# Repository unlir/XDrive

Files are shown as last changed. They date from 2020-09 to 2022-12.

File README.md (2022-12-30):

# XDrive 
Stepper motor with multi-function interface and closed loop function.  
具有多功能接口和闭环功能的步进电机。
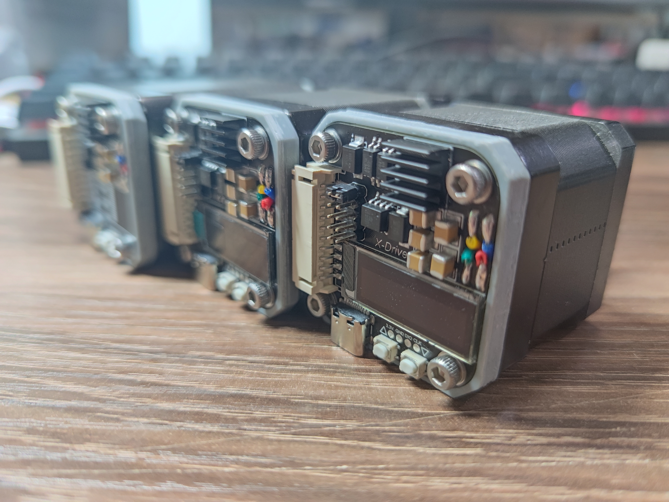
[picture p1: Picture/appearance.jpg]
appearance icon


## 版本更新日志
### 2021/01/03
1.避开了上电后第一次读取编码器错误数据造成的启动抖动（本质问题未解决）  
2.修正了控制器初始化错误造成的启动抖动（本质还是因为第一条的原因）  
3.XDrive_BL升级到F1.2版本，仅使用UP按键作为升级按键  
4.修正了一些讲不清道不明的BUG  
5.XDrive项目讨论可加群（3群：1105302151）（2群：1105489563）（1群：557214000）

## 目录简介
Firmware_APP：主要的控制固件（XDrive_APP.uvprojx 为主应用工程） 
Firmware_BL：引导固件（用于引导USB更新）  
Hardware：电路图纸  
Machinery：外壳图纸  
Picture：XDrive照片  
Specification：使用及入门介绍

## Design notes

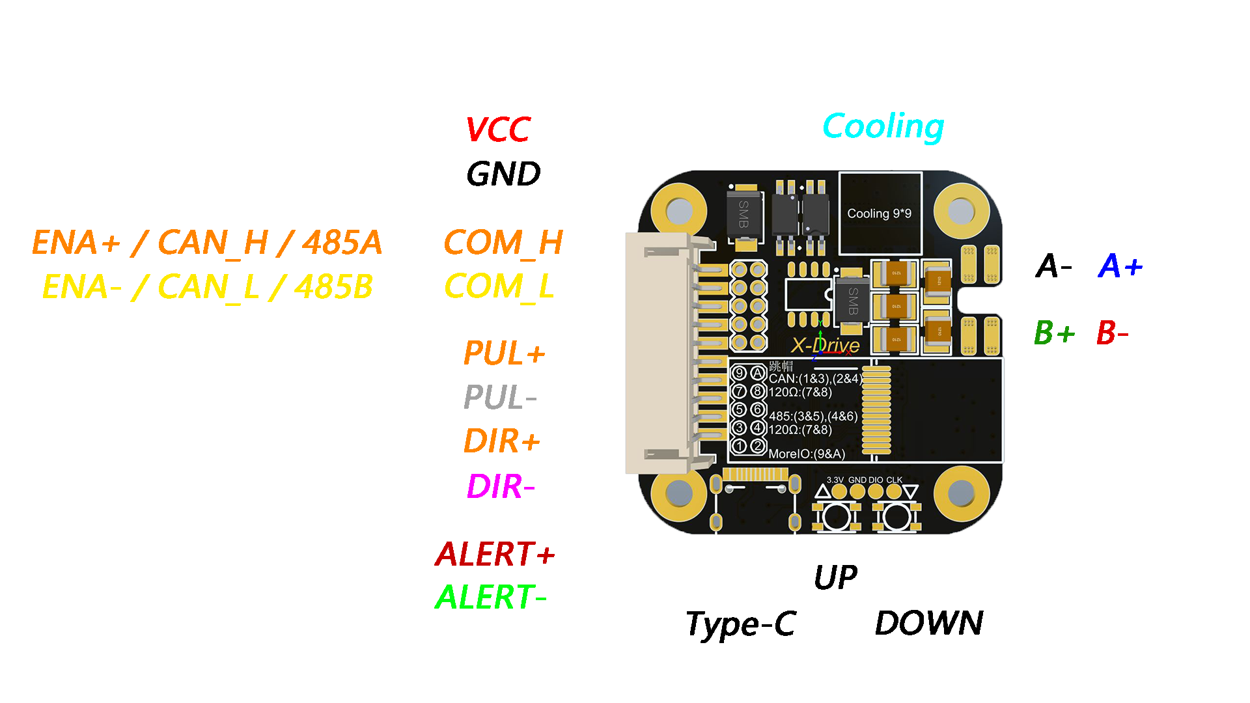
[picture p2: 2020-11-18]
Specification/输入输出标注.png

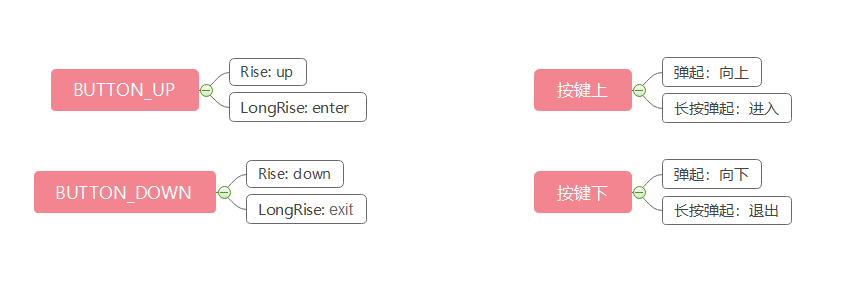
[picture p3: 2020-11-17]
Specification/Button.png

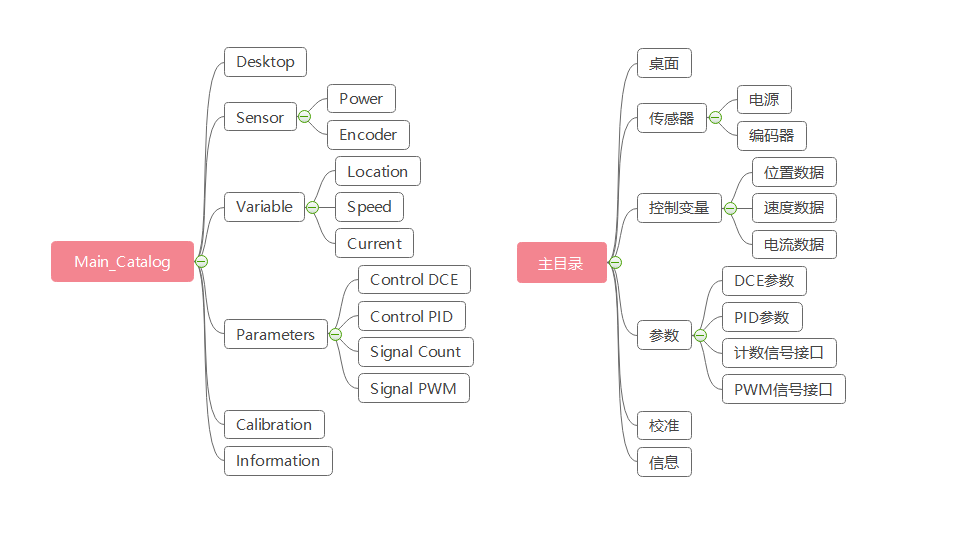
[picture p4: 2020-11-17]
Specification/UI Logic.png

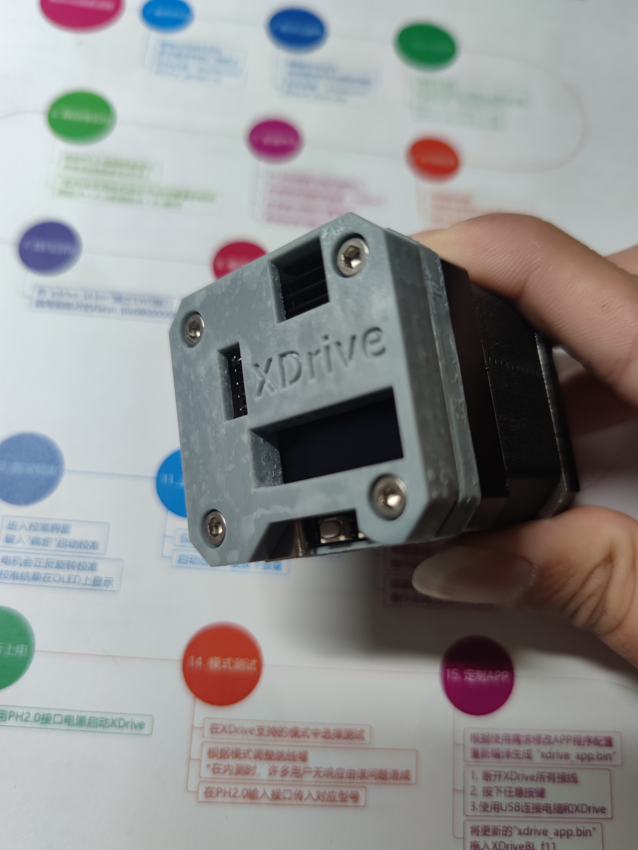
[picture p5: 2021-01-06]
Picture/shell.jpg

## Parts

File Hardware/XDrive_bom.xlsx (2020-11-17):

Comment | Description | Designator | Footprint | LibRef | Quantity | Pins
20pF (200) 5% 50V | 贴片电容 | C1, C2 | 0603_C | 0603 20pF (200) 5% 50V | 2 | 2
100nF (104) 10% 50V | 贴片电容 | C3, C4, C5, C6, C7, C8, C9, C10, C11, C12, C13, C14, C16, C17, C18, C19, C21, C22, C27, C29 | 0603_C | 0603 100nF (104) 10% 50V | 20 | 2
10uF (106) 10% 10V | 贴片电容 | C15, C23, C28, C30, C35, C36, C37, C38 | 0603_C | 0603 10uF (106) 10% 10V | 8 | 2
100pF (101) 5% 50V | 贴片电容 | C20 | 0603_C | 0603 100pF (101) 5% 50V | 1 | 2
47uF (106) 20% 10V | 贴片电容 | C24 | 1206_C | 1206 10uF (106) 10% 50V | 1 | 2
4.7uF (475) 10% 50V | 贴片电容 | C25 | 1206_C | 1206 4.7uF (475) 10% 50V | 1 | 2
1uF (105) 10% 16V | 贴片电容 | C31, C32, C33, C34 | 0603_C | 0603 1uF (105) 10% 50V | 4 | 2
100uF (107) 20% 50V | 贴片电容 | C41, C42, C43, C44, C45 | C 1210_L | Cap | 5 | 2
NC | 贴片电容 | C46, C47, C48 | C 1210_L | Cap | 3 | 2
双排插针-2X5P | 双排插针-2.0mm | CN1 | A2005WV-2X5P | A2005WV-2X5P | 1 | 10
SESD3Z12C | 双向ESD | D1, D2 | SOD-323 | SESD3Z12C | 2 | 2
SS54 | 二极管 | D3 | SMB | SMA(DO-214AC) SS54 | 1 | 2
B5819WS | 二极管 | D4, D6 | SOD-323 | SOD-323 1N4148WS T4 | 2 | 2
SMBJ28CA | TVS | D5 | SMB | SMB/DO-214AA P6SMB6.8CA | 1 | 2
SMD0805-020 | 自恢复保险丝 200mA | F1, F2 | FU 0805 | Fuse 2 | 2 | 2
SMD0805-050 | 自恢复保险丝 500mA | F3 | FU 0805 | Fuse 2 | 1 | 2
6.8UH 6R6 | 贴片电感 | L1 | L 1206 | IND | 1 | 2
OLED12832 | OLED焊接座 | L2 | PCBComponent_1 - duplicate | OLED12832 | 1 | 15
10KΩ (1002) ±1% | 贴片电阻 | R1, R2, R9, R24 | 0603_R | 0603 10KΩ (1002) 1% | 4 | 2
1KΩ (1001) ±1% | 贴片电阻 | R3, R4, R6, R7, R10, R14, R15, R17 | 0603_R | 0603 1KΩ (1001) 1% | 8 | 2
0.1Ω (R100) ±1% | 贴片电阻 | R5, R8 | 1206_R | 1206 0.1Ω (R100) 1% | 2 | 2
200Ω (2000) ±1% | 贴片电阻 | R11, R13, R16, R18 | 0603_R | 0603 200Ω (2000) 1% | 4 | 2
120Ω (1200) ±1% | 贴片电阻 | R12 | 0805_R | 0805 120Ω (1200) 1% | 1 | 2
22Ω (22R0) ±1% | 贴片电阻 | R19, R20 | 0603_R | 0603 22Ω (22R0) 1% | 2 | 2
1.5KΩ (1501) ±1% | 贴片电阻 | R21 | 0603_R | 0603 1.5KΩ (1501) 1% | 1 | 2
12KΩ (1202) ±1% | 贴片电阻 | R22, R23 | 0603_R | 0603 12KΩ (1202) 1% | 2 | 2
1.91KΩ (1901) ±1% | 贴片电阻 | R25 | 0603_R | 0603 1KΩ (1001) 1% | 1 | 2
1MΩ (1004) ±1% | 贴片电阻 | R26, R27 | 0603_R | 0603 1MΩ (1004) 1%, 0603 2MΩ (2004) 1% | 2 | 2
SKRPABE010 | 4脚贴片按键 | SW1, SW2 | KEY-SMD-4P_L4.20-W3.20 | SKRPABE010 | 2 | 4
STM32F103CBT6 | STM32 ARM-based 32-bit MCU Performance Line with 128 kB Flash, 20 kB Internal RAM, -40 to +85癈 Temperature, 48-Pin LQFP, Tray | U1 | LQFP48_N | STM32F103CBT6 | 1 | 48
TB67H450 | 直流电机驱动器 | U2, U3 | SOIC-8_EP_150MIL | A4950ELJTR-T | 2 | 9
MT6816 | 磁角度传感器 | U4 | SOIC_8 | MT6816 | 1 | 8
A2001WR-S-10PD01 | 贴片PH2.0插座 | U5 | PH2.0-WS-10P | A2001WR-S-10PD01 | 1 | 11
EL3H7(B)(TA)-G | 光耦 | U6, U7 | SOP4 | EL357N(A)(TA)-G | 2 | 4
EL0631 | 光耦 | U8 | SOIC-8_L5.0-W4.0-P1.27-LS6.0-BL | TLP2160(TP,F) | 1 | 8
SN75176BDR | RS-485/RS-422 | U9 | SOIC_8 | SN75176BDR_[C7063] | 1 | 8
CAN/TJA1051T/3 | CAN | U10 | SOIC_8 | CAN/TJA1051T/3_[C38695] | 1 | 8
ME3116AM6G | DC-DC芯片 | U11 | SOT-23-6 | MP2451DT-LF-Z_[C14123] | 1 | 6
TYPE-C-31-M-12 | TYPE-C USB插座 | USBC1 | USB-C_SMD-TYPE-C-31-M-12 | TYPE-C-31-M-12 | 1 | 18
ME6206A33M3G | 低压差线性稳压(LDO) | VR1 | SOT-23-3L | SOT-23 XC6206P332MR | 1 | 3
12MHZ 20PF 10PPM | 贴片晶振 | Y1 | SMD-3225_4P | SMD-3225_4P 12MHZ 20PF 10PPM | 1 | 4

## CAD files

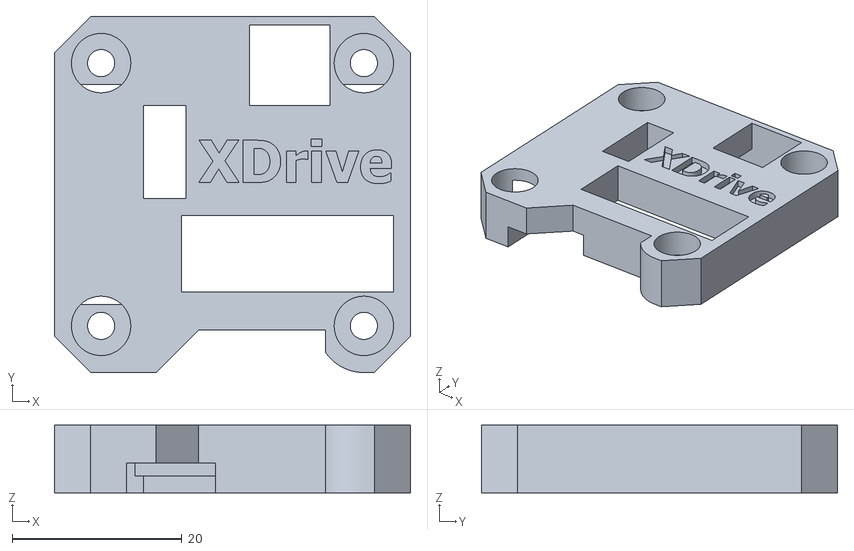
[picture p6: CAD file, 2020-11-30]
Machinery/顶盖-20201125.STL
42.0 x 42.0 x 8.00

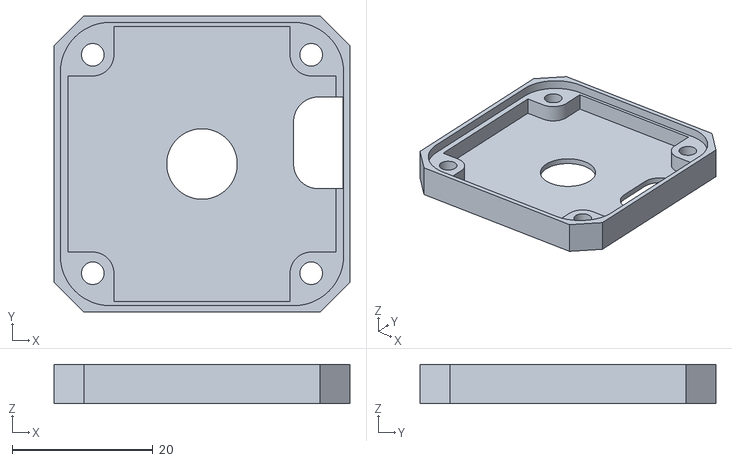
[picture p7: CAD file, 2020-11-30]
Machinery/底座-20201125.STL
42.0 x 42.0 x 5.60

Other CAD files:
Machinery/底座.SLDPRT
Machinery/顶盖.SLDPRT

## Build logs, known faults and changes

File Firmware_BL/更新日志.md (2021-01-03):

# XDrive_BL_F1.1
# 2020.12.8 首次发布
# 1.进入BT的方法（按下UP或者DOWN按键上电）
#
# XDrive_BL_F1.2
# 2020.12.8 更新
# 1.进入BT的方法（按下UP按键上电）
#
#
#

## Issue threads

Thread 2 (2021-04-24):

关于CAN通信问题

SamFisher940425, 2021-04-24:
简单查看代码发现LOOP当中通信接口初始化仅对UART（485modbus）进行了操作，CAN口是否启用了？能否简单分享一下can或modbus通信协议

Joelliamliu, 2022-08-18:
> 简单查看代码发现LOOP当中通信接口初始化仅对UART（485modbus）进行了操作，CAN口是否启用了？能否简单分享一下can或modbus通信协议，十分感谢！

同问，想用CAN单独调试电机，但没有通讯报文说明

SamFisher940425, 2022-08-18:
> 原作者可能比较忙，CAN部分还是自行编写吧。另外，原作者有闭源方案，可以考虑使用。

Joelliamliu, 2022-08-20:
> > 原作者可能比较忙，CAN部分还是自行编写吧。另外，原作者有闭源方案，可以考虑使用。

谢谢

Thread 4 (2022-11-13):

两颗独立的 TB67H450FNG 驱动步进电机需要同步机制吗？

zhbi98, 2022-11-13:
### 概述

通过 TB67H450FNG 的数据手册知道该芯片是仅有一个通道的有刷直流电机驱动芯片，意味着用于驱动两相步进电机需要使用两颗 TB67H450FNG 芯片。

### 疑问

42 步进电机是两相的，所以就需要两颗 TB67H450FNG 芯片交替有序的输出，所以不知道这两颗芯片如何有序同步，或是说输出信号的相位是否需要错开。

很期待能够得到大佬的解答，在此提前谢过能够解惑的大佬。

Mountain03, 2022-12-15:
直接看源码,能看懂

Closed 2022-12-16.

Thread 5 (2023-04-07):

关于DCE的问题

Silence-creat, 2023-04-07:
新手在研究步进电机，您这里在关于步进电机的控制中使用了DCE的控制，  我在网上检索资料很难检索到而还有相同缩写的DCE控制（是一种利用协方差矩阵进行速度和位置控制的方法）。您能简单的描述一下您程序中使用的DCE控制方法是指什么吗？或者分享一些相关的资料，说实话我很难查到，论文和chartgpt我都有进行过检索并没有能够给我准确的信息。还望您赐教。

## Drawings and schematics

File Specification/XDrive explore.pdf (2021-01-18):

## 完全DIY (从流程1开始)

## 购买独立主板 (从流程4开始)

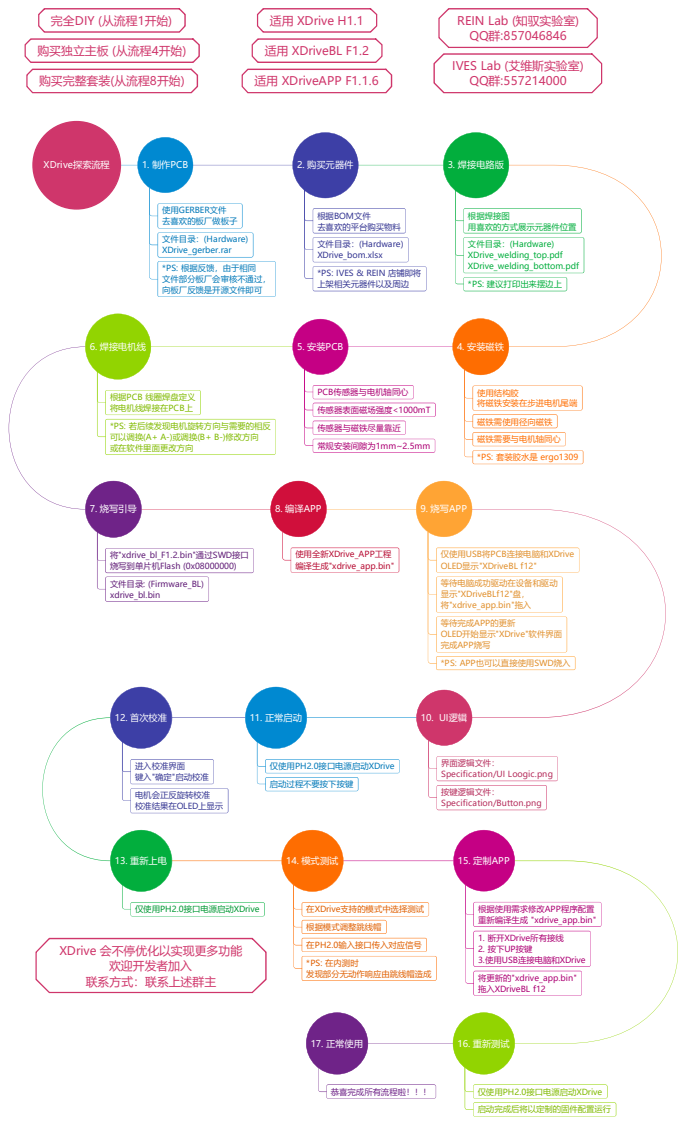
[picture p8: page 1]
XDrive探索流程; 1. 制作PCB; 6. 焊接电机线; 5. 安装PCB; 7. 烧写引导; 2. 购买元器件; 3. 焊接电路版; 4. 安装磁铁; 8. 编译APP; 9. 烧写APP; 12. 首次校准; 11. 正常启动; 10. UI逻辑; 13. 重新上电; 14. 模式测试; 15. 定制APP; 16. 重新测试; 使用GERBER文件 去喜欢的板厂做板子; 文件目录：(Hardware) XDrive_gerber.rar; 根据焊接图 用喜欢的方式展示元器件位置; PCB传感器与电机轴同心; 传感器表面磁场强度<1000mT; 将"xdrive_bl_F1.2.bin"通过SWD接口 烧写到单片机Flash (0x08000000); 使用全新XDrive_APP工程 编译生成"xdrive_app.bin"; 进入校准界面; 仅使用PH2.0接口电源启动XDrive; 在XDrive支持的模式中选择测试; 在PH2.0输入接口传入对应信号; 根据使用需求修改APP程序配置 重新编译生成 "xdrive_app.bin"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

REIN Lab (知驭实验室)
QQ群:857046846

IVES Lab (艾维斯实验室)
QQ群:557214000

根据BOM文件
去喜欢的平台购买物料
文件目录：(Hardware)
XDrive_bom.xlsx
*PS: IVES & REIN 店铺即将

根据PCB 线圈焊盘定义
将电机线焊接在PCB上
*PS: 若后续发现电机旋转方向与需要的相反
可以调换(A+ A-)或调换(B+ B-)修改方向
或在软件里面更改方向

仅使用USB将PCB连接电脑和XDrive
OLED显示"XDriveBL f12"
等待电脑成功驱动在设备和驱动
显示"XDriveBLf12"盘，
将"xdrive_app.bin"拖入
等待完成APP的更新
OLED开始显示"XDrive"软件界面
完成APP烧写
*PS: APP也可以直接使用SWD烧入

界面逻辑文件：
Specification/UI Loogic.png
按键逻辑文件：
Specification/Button.png

键入"确定"启动校准
电机会正反旋转校准
校准结果在OLED上显示

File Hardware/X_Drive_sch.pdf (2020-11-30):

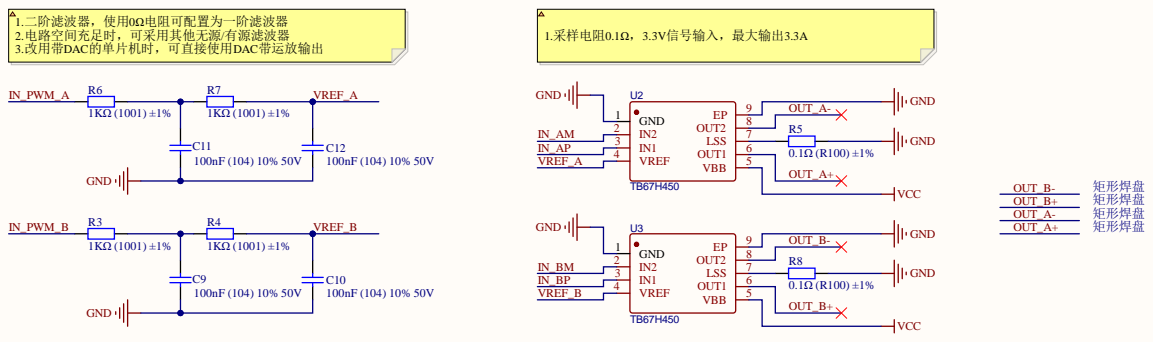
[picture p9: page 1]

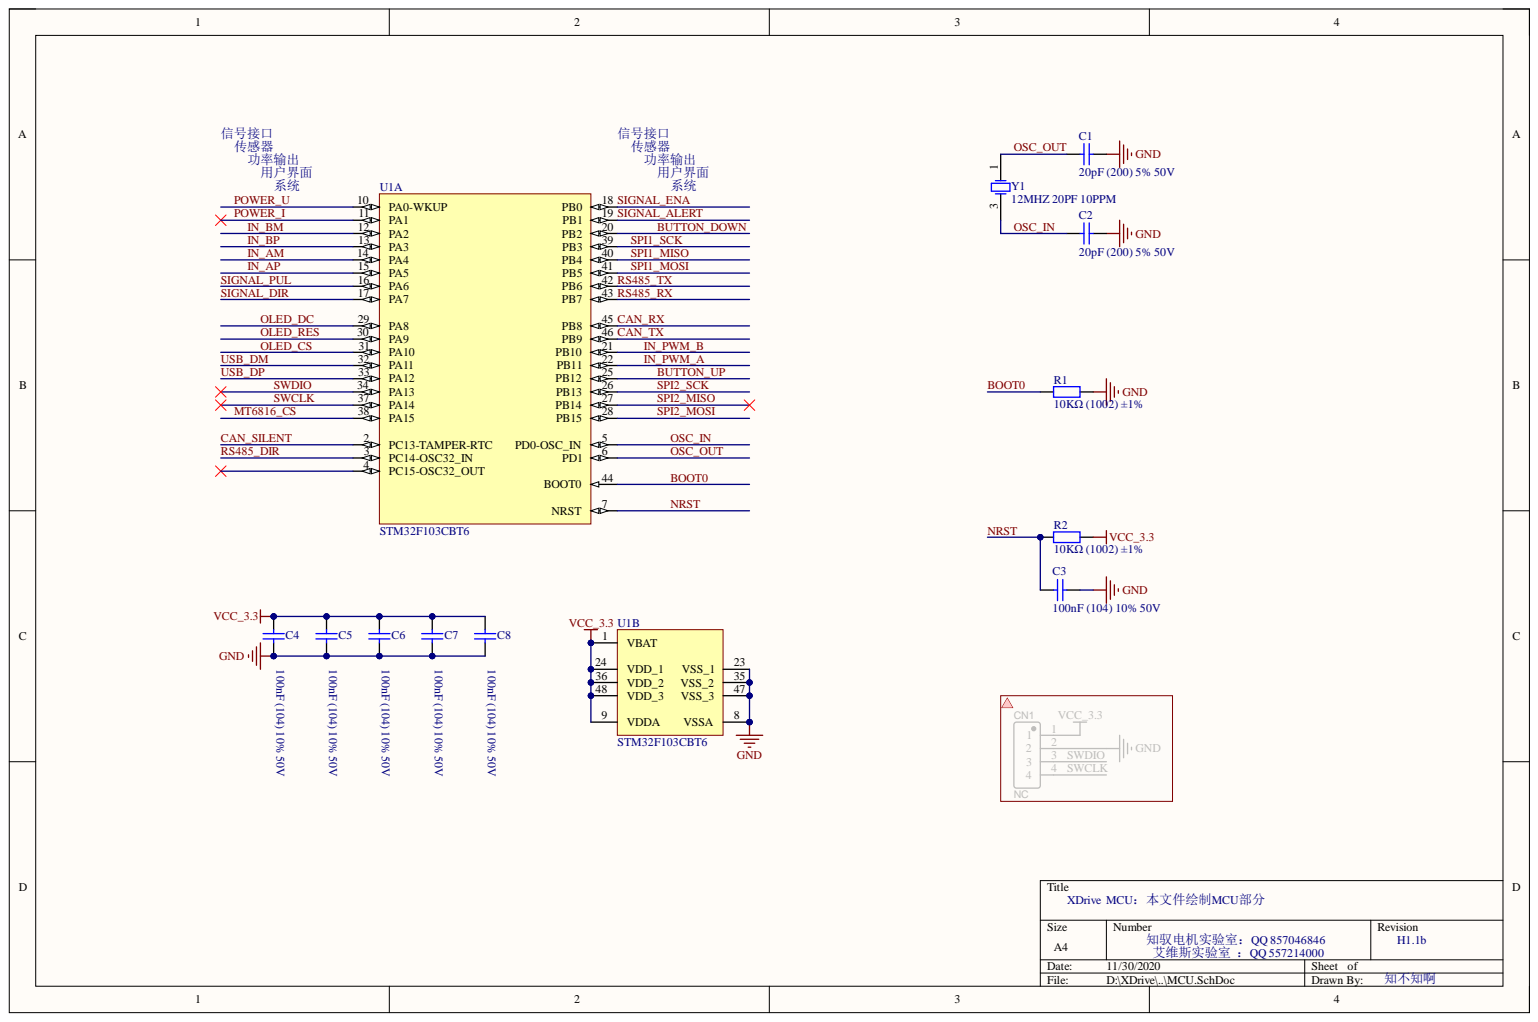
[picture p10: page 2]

3 6 | 3 5
4 8 | 4 7

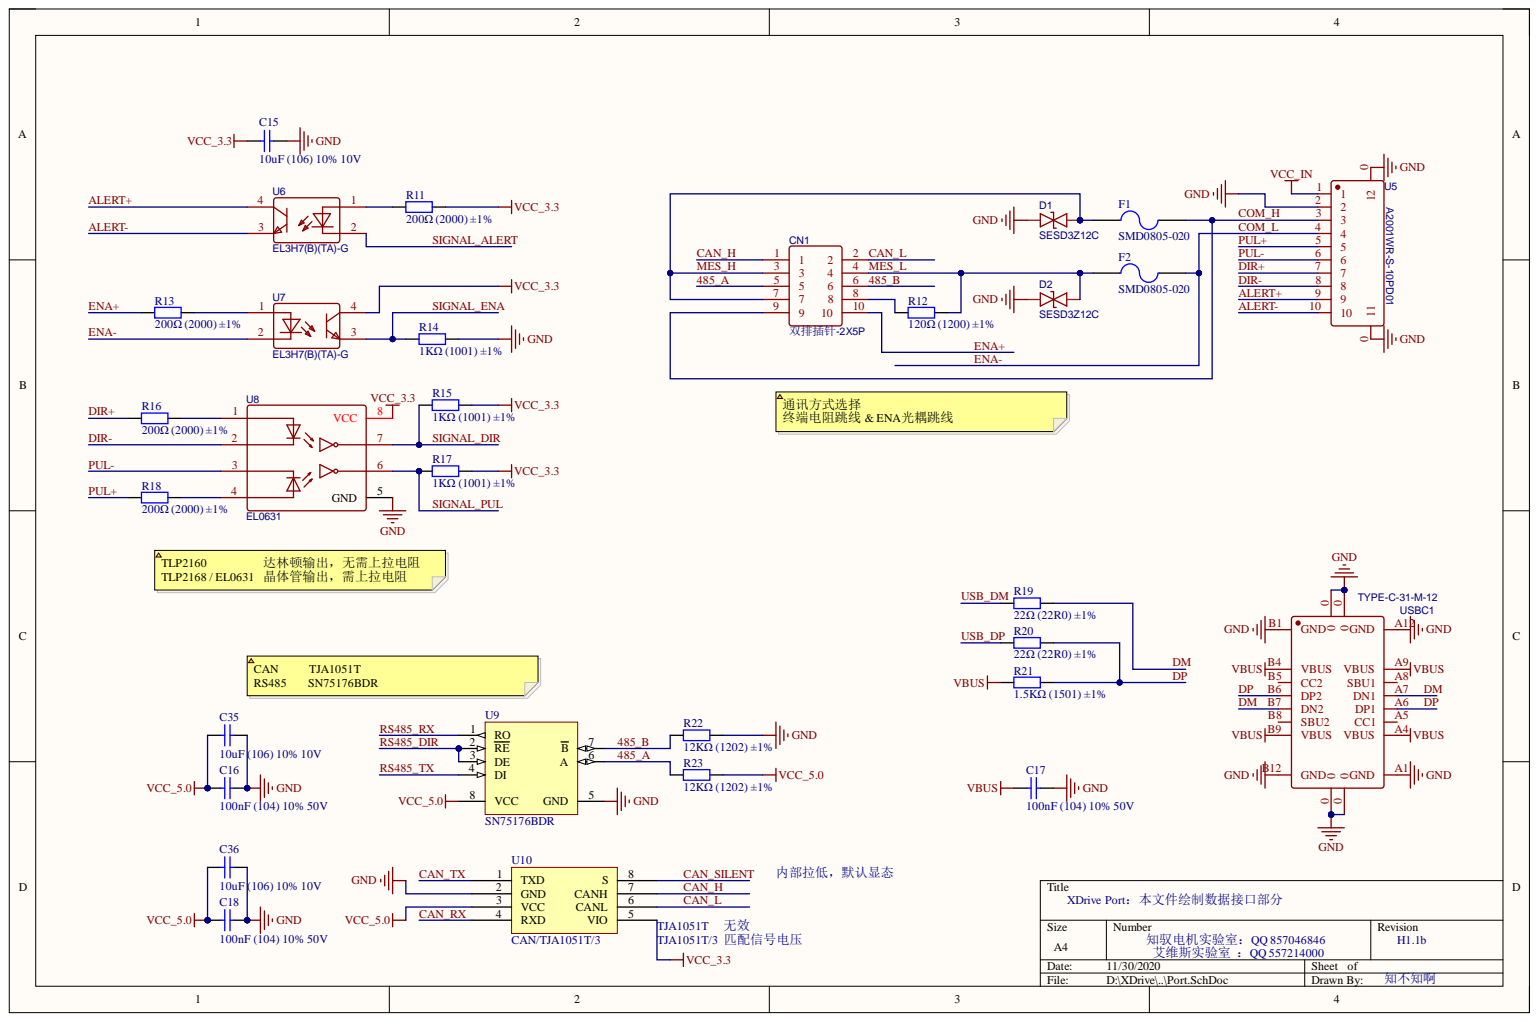
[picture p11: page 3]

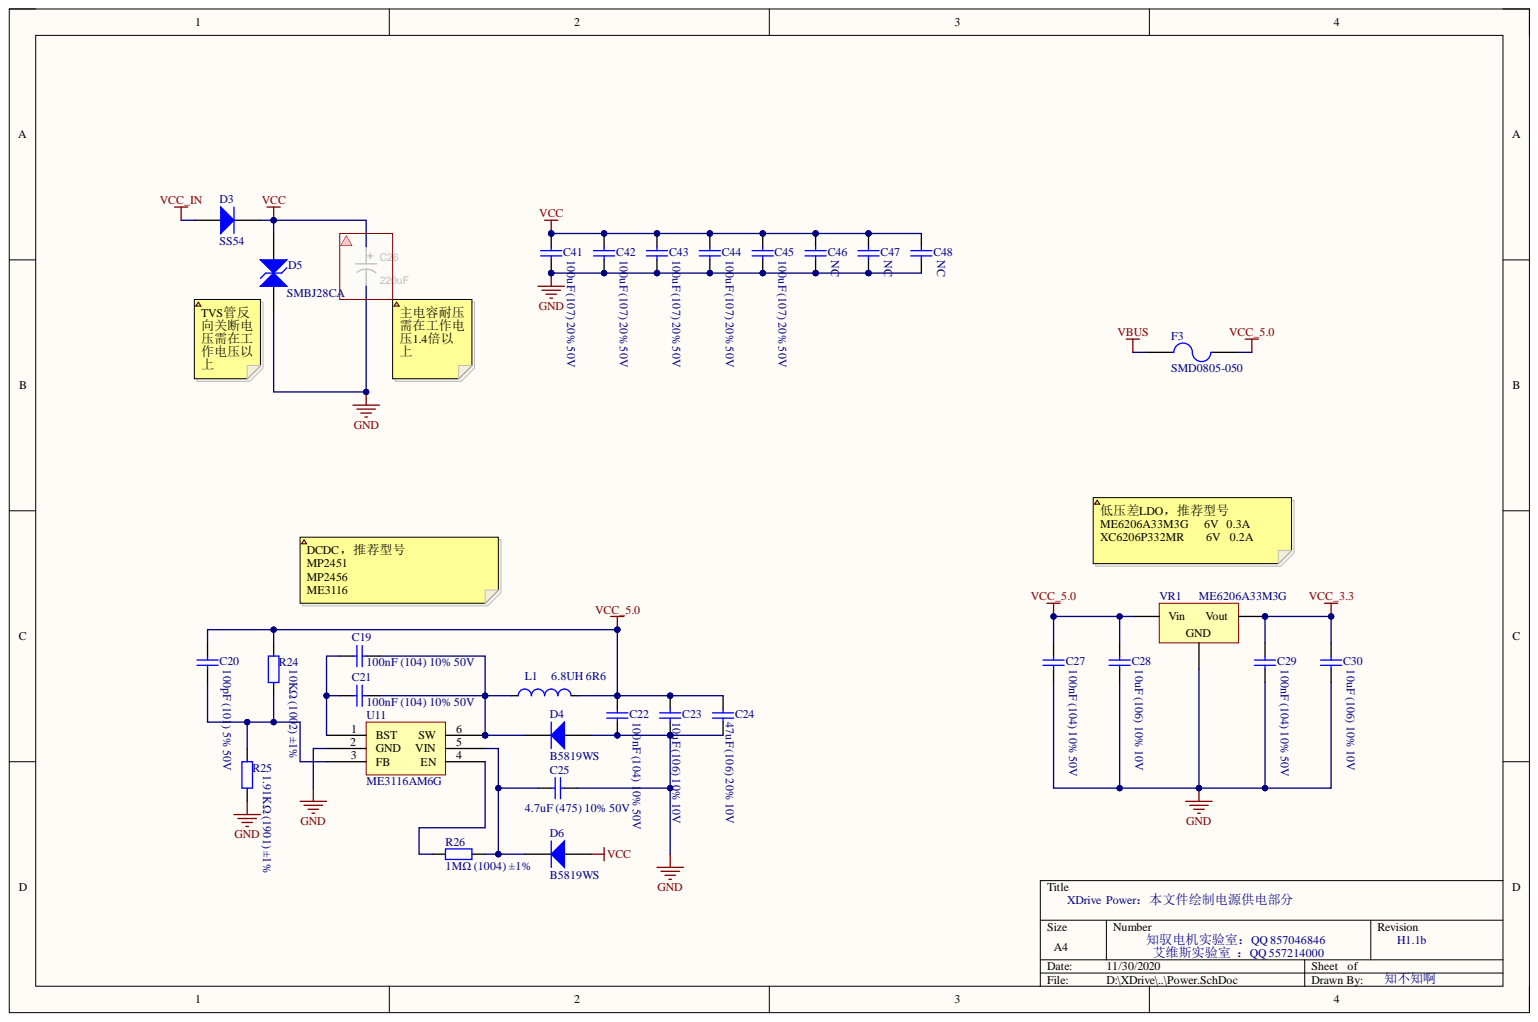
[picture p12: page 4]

U11
BST 1

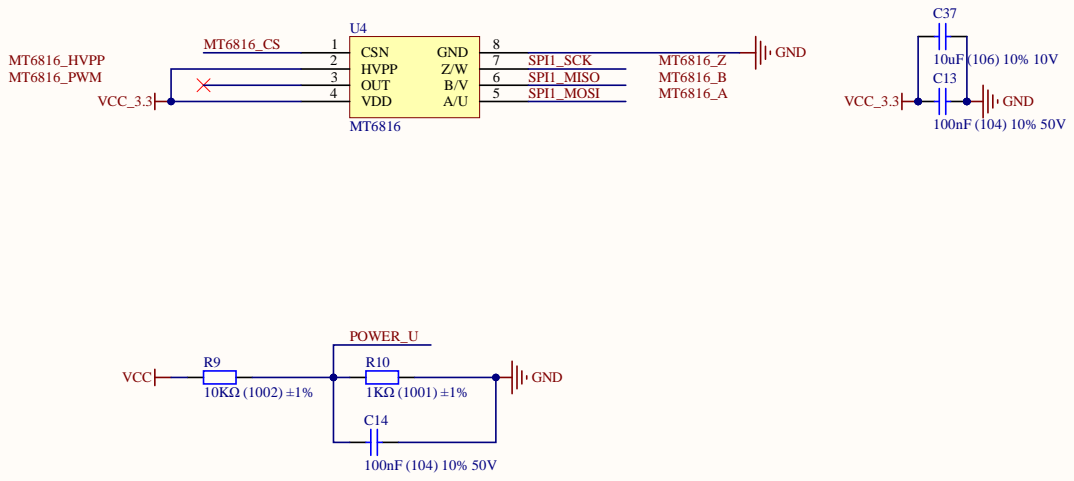
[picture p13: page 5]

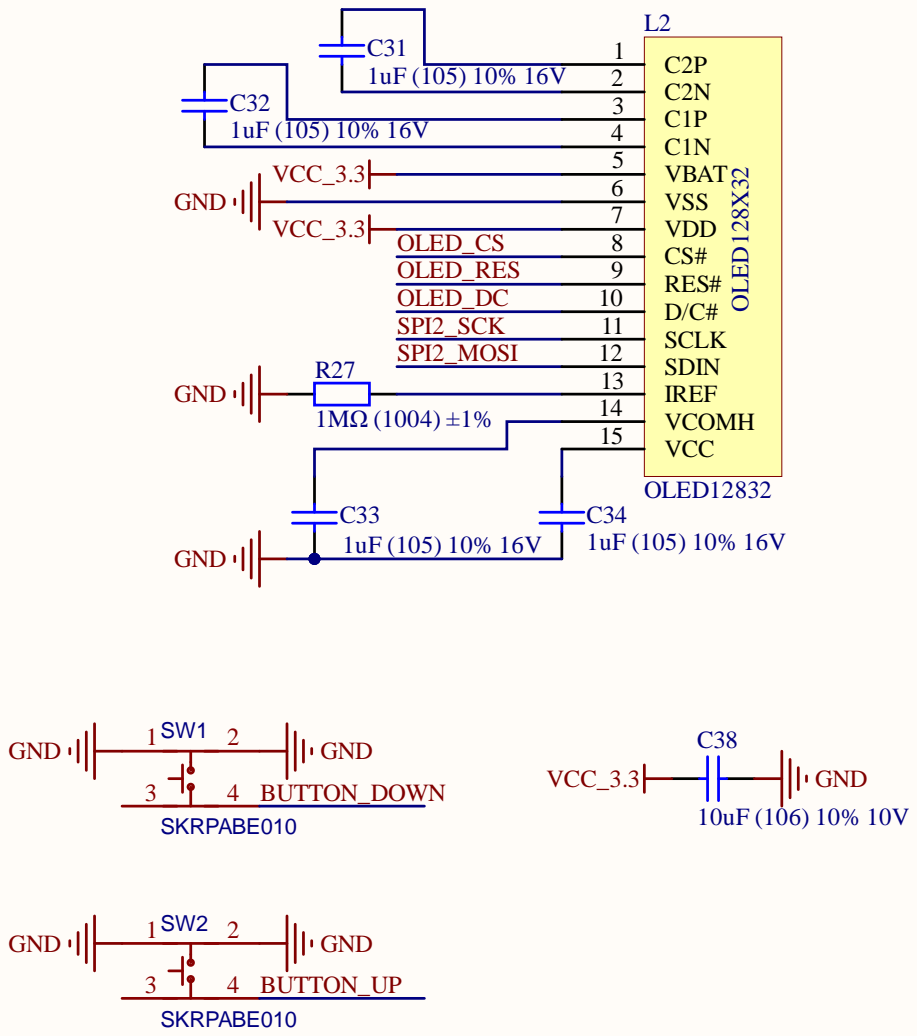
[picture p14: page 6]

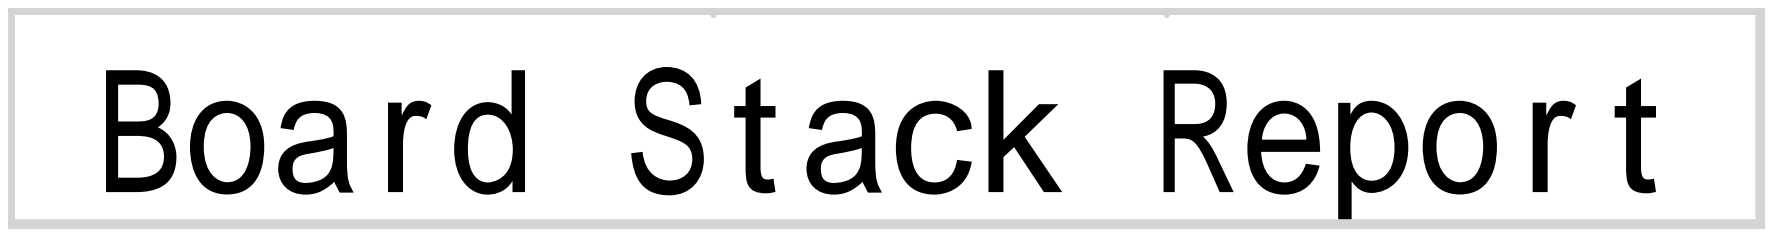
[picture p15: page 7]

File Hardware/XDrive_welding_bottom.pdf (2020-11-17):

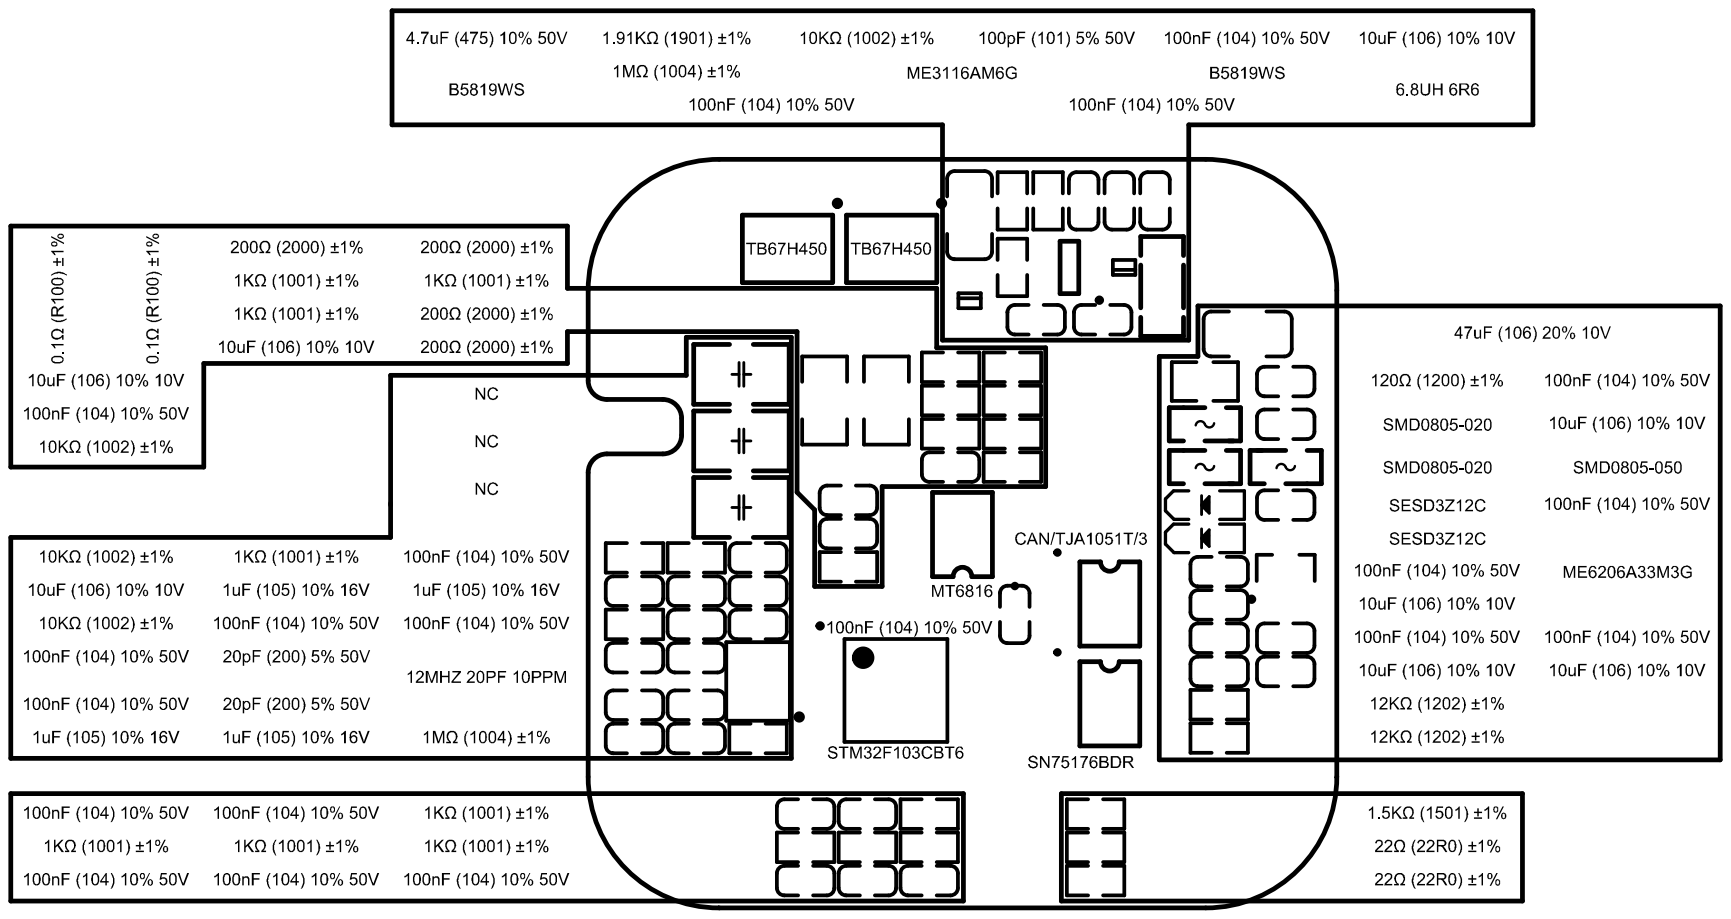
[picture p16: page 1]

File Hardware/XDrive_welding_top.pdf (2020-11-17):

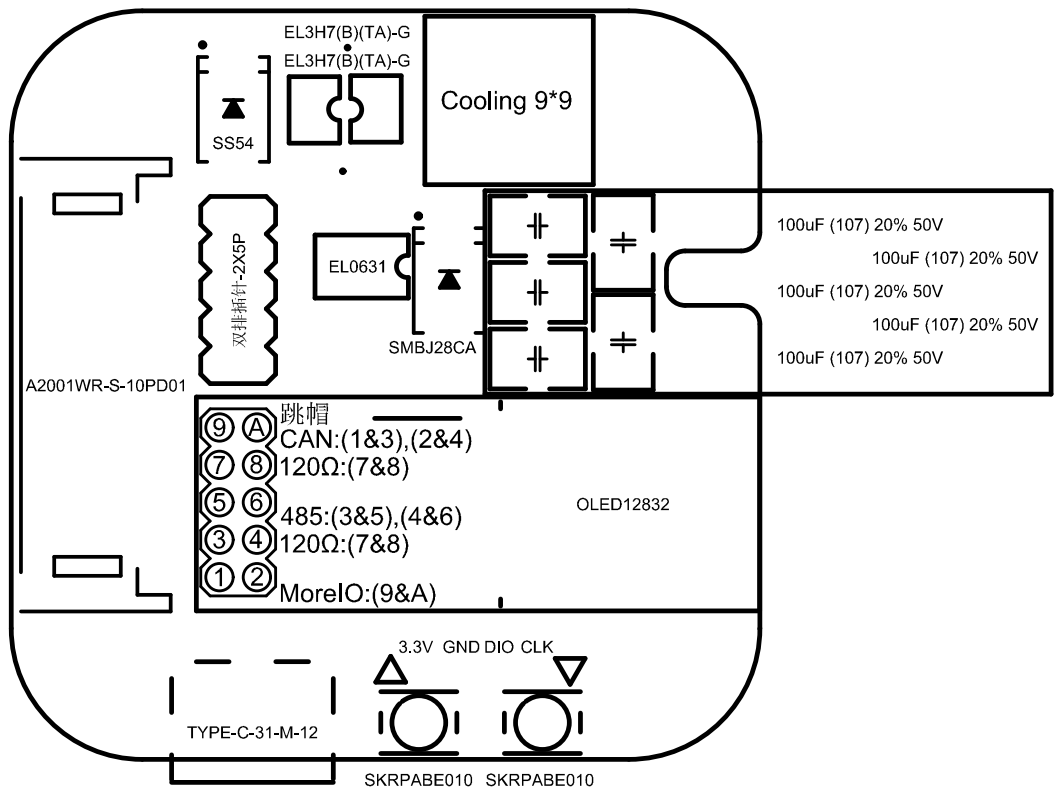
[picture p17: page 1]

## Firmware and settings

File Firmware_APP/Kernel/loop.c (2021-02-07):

/******
	************************************************************************
	******
	** @project : XDrive_Step
	** @brief   : Stepper motor with multi-function interface and closed loop function. 
	** @brief   : 具有多功能接口和闭环功能的步进电机
	** @author  : unlir (知不知啊)
	** @contacts: QQ.1354077136
	******
	** @address : https://github.com/unlir/XDrive
	******
	************************************************************************
	******
	** {Stepper motor with multi-function interface and closed loop function.}
	** Copyright (c) {2020}  {unlir(知不知啊)}
	** 
	** This program is free software: you can redistribute it and/or modify
	** it under the terms of the GNU General Public License as published by
	** the Free Software Foundation, either version 3 of the License, or
	** (at your option) any later version.
	** 
	** This program is distributed in the hope that it will be useful,
	** but WITHOUT ANY WARRANTY; without even the implied warranty of
	** MERCHANTABILITY or FITNESS FOR A PARTICULAR PURPOSE.  See the
	** GNU General Public License for more details.
	** 
	** You should have received a copy of the GNU General Public License
	** along with this program.  If not, see <http://www.gnu.org/licenses/>.
	******
	************************************************************************
******/

/*****
  ** @file     : loop.c/h and loop_it.c
  ** @brief    : MCU系工程主框架
  ** @versions : newest
  ** @time     : newest
  ** @reviser  : unli (WuHu China)
  ** @explain  : null
*****/

//Oneself
#include "loop.h"

//Application_User_Core
#include "dma.h"
#include "adc.h"
#include "usart.h"

//Base_Drivers
#include "kernel_port.h"
#include "mt6816.h"
#include "hw_elec.h"

//Control
#include "signal_port.h"
#include "motor_control.h"
#include "encode_cali.h"

//Debug
#include "button.h"
#include "ssd1306.h"
#include "xdrive_ui.h"

/**********************************************************************/
/*********************    Subclock processing    **********************/
/**********************************************************************/
uint32_t time_1ms_count = 0;
uint32_t major_cycle_count = 0;
static uint32_t time_second_1ms = 0;
static uint32_t time_second_10ms = 0;
static uint32_t time_second_20ms = 0;
static uint32_t time_second_50ms = 0;
static uint32_t time_second_100ms = 0;

/**
* @brief 副时钟10ms执行
*/
void time_second_10ms_serve(void)
{

}

/**
* @brief 副时钟20ms执行
*/
void time_second_20ms_serve(void)
{
	//XDrive_REINui(50Hz刷新率)
	XDrive_REINui_Callback_ms(20);
}

/**
* @brief 副时钟50ms执行
*/
void time_second_50ms_serve(void)
{

}

/**
* @brief 副时钟100ms执行
*/
void time_second_100ms_serve(void)
{

}
	
/**
* @brief 副时钟循环执行
**/
void time_second_run(void)
{
	if(time_second_10ms)		{time_second_10ms--;		time_second_10ms_serve();		}
	if(time_second_20ms)		{time_second_20ms--;		time_second_20ms_serve();		}
	if(time_second_50ms)		{time_second_50ms--;		time_second_50ms_serve();		}
	if(time_second_100ms)		{time_second_100ms--;		time_second_100ms_serve();	}
}

/**
* @brief 副时钟1ms时钟
**/
void loop_second_base_1ms(void)
{
	time_1ms_count++;
	time_second_1ms++;
	if(!(time_second_1ms % 10))		{time_second_10ms++;		}
	if(!(time_second_1ms % 20))		{time_second_20ms++;		}
	if(!(time_second_1ms % 50))		{time_second_50ms++;		}
	if(!(time_second_1ms % 100))	{time_second_100ms++;		}
	if(!(time_second_1ms % 1000))	{time_second_1ms = 0;		}
}

/*********************************************************************/
/****************************    LOOP    *****************************/
/*********************************************************************/
/**
* This is Main LOOP
*/
void loop(void)
{
	//调试工具(Debug)
	Button_Init();				//按键初始化
	SSD1306_Init();				//OLED初始化
	XDrive_REINui_Init();	//UI初始化
	
	//进行关键外设初始化前等待电源稳定
	HAL_Delay(1000);
	
//	//存储数据恢复
//	Slave_Reg_Init();			//校验Flash数据并配置参数
	
	//基本外设初始化(Base_Drivers)(LOOP直接进行)
	REIN_DMA_Init();
	REIN_ADC_Init();	
	
	//基本外设初始化()
	REIN_MT6816_Init();		//MT6816传感器初始化
	REIN_HW_Elec_Init();	//硬件电流控制器
	Signal_MoreIO_Init();	//MoreIO接口初始化
	
	//控制初始化(Control)
	Calibration_Init();		//校准器初始化
	Motor_Control_Init();	//电机控制初始化
	
	//通讯接口初始化
	REIN_GPIO_Modbus_Init();	//RS485_DIR
	REIN_UART_Modbus_Init();	//串口初始化
	Signal_Modbus_Init();			//Modbu接口初始化
	
	//调整中断配置
	LoopIT_Priority_Overlay();	//重写-中断优先级覆盖
	LoopIT_SysTick_20KHz();			//重写-系统计时器修改为20KHz
	
	//启动时使用按键触发校准
	if(HAL_GPIO_ReadPin(BUTTON_DOWN_GPIO_Port, BUTTON_DOWN_Pin) == GPIO_PIN_RESET)
	{
		encode_cali.trigger = true;			//触发校准
		XDrive_REINui_ToCalibration();	//进入UI校准界面
	}
	
	//FOR Circulation
	for(;;)
	{
		major_cycle_count++;
		time_second_run();

		Calibration_Loop_Callback();							//校准器主程序回调					用于校准环节最后的数据解算
	}
}
/*************************************
*********** END Dispatch  ************
*************************************/

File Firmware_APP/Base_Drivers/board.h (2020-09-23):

/******
	************************************************************************
	******
	** @versions : 1.1.4
	** @time     : 2020/09/15
	******
	************************************************************************
	******
	** @project : XDrive_Step
	** @brief   : 具有多功能接口和闭环功能的步进电机
	** @author  : unlir (知不知啊)
	******
	** @address : https://github.com/unlir/XDrive
	******
	** @issuer  : IVES ( 艾维斯 实验室) (QQ: 557214000)   (master)
	** @issuer  : REIN (  知驭  实验室) (QQ: 857046846)   (master)
	******
	************************************************************************
	******
	** {Stepper motor with multi-function interface and closed loop function.}
	** Copyright (c) {2020}  {unlir}
	** 
	** This program is free software: you can redistribute it and/or modify
	** it under the terms of the GNU General Public License as published by
	** the Free Software Foundation, either version 3 of the License, or
	** (at your option) any later version.
	** 
	** This program is distributed in the hope that it will be useful,
	** but WITHOUT ANY WARRANTY; without even the implied warranty of
	** MERCHANTABILITY or FITNESS FOR A PARTICULAR PURPOSE.  See the
	** GNU General Public License for more details.
	** 
	** You should have received a copy of the GNU General Public License
	** along with this program.  If not, see <http://www.gnu.org/licenses/>.
	******
	************************************************************************
******/

/*****
  ** @file     : kernel_port.c/h
  ** @brief    : 端口定义
  ** @versions : newest
  ** @time     : newest
  ** @reviser  : unli (HeFei China)
  ** @explain  : null
*****/

#ifndef KERNEL_PORT_H
#define KERNEL_PORT_H

#ifdef __cplusplus
extern "C" {
#endif

//C基本库
#include <stdint.h>		//基本数据类型
#include <stdbool.h>	//Bool数据类型
#include <string.h>		//变量类型,宏,字符数组函数
#include <stdlib.h>		//变量类型,宏,通用工具函数
#include <stdio.h>		//变量类型,宏,输入输出函数

//HAL库引用
#include "main.h"
#include "gpio.h"
#include "spi.h"
#include "tim.h"

//HAL库函数引用
#define MEIN_Delay_MS(ms)		HAL_Delay(ms)

/********** A **********/

/********** B **********/
/********** BUTTON **********/
/********** BUTTON **********/
/********** BUTTON **********/
//(GPIO)
#define BUTTON_OK_GPIO_CLK_ENABLE()			__HAL_RCC_GPIOA_CLK_ENABLE();		//PA2
#define BUTTON_OK_GPIO_Port							(GPIOA)
#define BUTTON_OK_Pin 									(GPIO_PIN_2)
#define BUTTON_UP_GPIO_CLK_ENABLE()			__HAL_RCC_GPIOA_CLK_ENABLE();		//PA3
#define BUTTON_UP_GPIO_Port							(GPIOA)
#define BUTTON_UP_Pin 									(GPIO_PIN_3)
#define BUTTON_DOWN_GPIO_CLK_ENABLE()		__HAL_RCC_GPIOC_CLK_ENABLE();		//PC13
#define BUTTON_DOWN_GPIO_Port						(GPIOC)
#define BUTTON_DOWN_Pin 								(GPIO_PIN_13)

/********** C **********/

/********** D **********/

/********** E **********/

/********** F **********/

/********** G **********/

/********** H **********/
/********** HW_ELEC **********/
/********** HW_ELEC **********/
/********** HW_ELEC **********/
//(GPIO)
#define HW_ELEC_AP_GPIO_CLK_ENABLE()		__HAL_RCC_GPIOB_CLK_ENABLE()		//PB1
#define HW_ELEC_AP_GPIO_Port						(GPIOB)
#define HW_ELEC_AP_Pin									(GPIO_PIN_1)
#define HW_ELEC_AM_GPIO_CLK_ENABLE()		__HAL_RCC_GPIOB_CLK_ENABLE()		//PB0
#define HW_ELEC_AM_GPIO_Port						(GPIOB)
#define HW_ELEC_AM_Pin									(GPIO_PIN_0)
#define HW_ELEC_BP_GPIO_CLK_ENABLE()		__HAL_RCC_GPIOC_CLK_ENABLE()		//PC14
#define HW_ELEC_BP_GPIO_Port						(GPIOC)
#define HW_ELEC_BP_Pin									(GPIO_PIN_14)
#define HW_ELEC_BM_GPIO_CLK_ENABLE()		__HAL_RCC_GPIOC_CLK_ENABLE()		//PC15
#define HW_ELEC_BM_GPIO_Port						(GPIOC)
#define HW_ELEC_BM_Pin									(GPIO_PIN_15)
//(AFIO & TIM)
#define HW_ELEC_APWM_GPIO_CLK_ENABLE()	__HAL_RCC_GPIOB_CLK_ENABLE()		//PB6
#define HW_ELEC_APWM_GPIO_Port					(GPIOB)
#define HW_ELEC_APWM_Pin								(GPIO_PIN_6)
#define HW_ELEC_APWM_CHANNEL						(TIM_CHANNEL_1)
#define HW_ELEC_BPWM_GPIO_CLK_ENABLE()	__HAL_RCC_GPIOB_CLK_ENABLE()		//PB7
#define HW_ELEC_BPWM_GPIO_Port					(GPIOB)
#define HW_ELEC_BPWM_Pin								(GPIO_PIN_7)
#define HW_ELEC_BPWM_CHANNEL						(TIM_CHANNEL_2)
#define HW_ELEC_PWM_TIM_CLK_ENABLE()		__HAL_RCC_TIM4_CLK_ENABLE()			//TIM4
#define	HW_ELEC_PWM_Get_TIM							(TIM4)
#define	HW_ELEC_PWM_Get_HTIM						(htim4)

/********** I **********/

/********** J **********/

/********** K **********/

/********** L **********/
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

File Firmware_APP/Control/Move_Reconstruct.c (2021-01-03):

/******
	************************************************************************
	******
	** @project : XDrive_Step
	** @brief   : Stepper motor with multi-function interface and closed loop function. 
	** @brief   : 具有多功能接口和闭环功能的步进电机
	** @author  : unlir (知不知啊)
	** @contacts: QQ.1354077136
	******
	** @address : https://github.com/unlir/XDrive
	******
	************************************************************************
	******
	** {Stepper motor with multi-function interface and closed loop function.}
	** Copyright (c) {2020}  {unlir(知不知啊)}
	** 
	** This program is free software: you can redistribute it and/or modify
	** it under the terms of the GNU General Public License as published by
	** the Free Software Foundation, either version 3 of the License, or
	** (at your option) any later version.
	** 
	** This program is distributed in the hope that it will be useful,
	** but WITHOUT ANY WARRANTY; without even the implied warranty of
	** MERCHANTABILITY or FITNESS FOR A PARTICULAR PURPOSE.  See the
	** GNU General Public License for more details.
	** 
	** You should have received a copy of the GNU General Public License
	** along with this program.  If not, see <http://www.gnu.org/licenses/>.
	******
	************************************************************************
******/

/*****
  ** @file     : Move_Reconstruct.c/h
  ** @brief    : 运动规划器
  ** @versions : 1.1.7
  ** @time     : 2019/12/06
  ** @reviser  : unli (JiXi XuanCheng China)
  ** @explain  : null
*****/

//Oneself
#include "Move_Reconstruct.h"

//Control.h
#include "Control_Config.h"

/****************************************  运动重构器  ****************************************/
/****************************************  运动重构器  ****************************************/
/****************************************  运动重构器  ****************************************/
//Move_Reconstruct实例
Move_Reconstruct_Typedef move_reco;

/**
  * 运动重构器设置减速加速度
  * @param  reconstruct		运动重构器实例
  * @retval true:成功 / false:错误
**/
void Move_Reconstruct_Set_DownAcc(int32_t value)
{
	value = abs(value);
	if((value > 0) && (value <= Move_Rated_DownAcc))
	{
		move_reco.down_acc = value;
		move_reco.valid_down_acc = true;
	}
	else{
		move_reco.valid_down_acc = false;
	}
}

/**
  * 运动重构器设置超时时间
  * @param  reconstruct		运动重构器实例
  * @retval true:成功 / false:错误
**/
void Move_Reconstruct_Set_OverTime(uint16_t value)
{
	if((value >= Reconstruct_Min_OverTime) && (value <= Reconstruct_Max_OverTime))
	{
		move_reco.overtime = value;
		move_reco.valid_overtime = true;
	}
	else{
		move_reco.valid_overtime = false;
	}
}

/**
  * 运动重构器参数恢复
  * @param  NULL
  * @retval NULL
**/
void Move_Reconstruct_Set_Default(void)
{
	Move_Reconstruct_Set_DownAcc(DE_DOWN_ACC);
	Move_Reconstruct_Set_OverTime(DE_OverTime);	
}

/**
  * 运动重构器初始化
  * @param  reconstruct		运动重构器实例
  * @retval NULL
**/
void Move_Reconstruct_Init(void)
{
	//前置配置无效时,加载默认配置
	if(!move_reco.valid_down_acc)	{	Move_Reconstruct_Set_DownAcc(DE_DOWN_ACC);	}
	if(!move_reco.valid_overtime)	{	Move_Reconstruct_Set_OverTime(DE_OverTime);	}
	
	//动态跟踪参数
	move_reco.dyn_speed_acc = 0;
	//源信号记录
	move_reco.record_timer = 0;
	move_reco.overtime_flag = false;
	move_reco.record_speed = 0;
	move_reco.record_location = 0;
	//计算过程数据
	move_reco.speed_course_dec = 0;
	move_reco.speed_course = 0;
	move_reco.location_course_dec = 0;
	move_reco.location_course = 0;
	//输出跟踪控制量
	move_reco.go_location = 0;
	move_reco.go_speed = 0;
}

/**
  * 运动重构器开始新任务
  * @param  reconstruct		运动重构器实例
  * @param  real_location	实时位置
  * @param  real_speed		实时速度
  * @retval NULL
**/
void Move_Reconstruct_NewTask(int32_t real_location, int32_t real_speed)
{
	//源信号记录
	move_reco.record_timer = 0;			//信号源计时器清零
	move_reco.overtime_flag = false;		//超时标志清位
	//更新计算过程数据
	move_reco.speed_course_dec = 0;				//过程速度
	move_reco.speed_course = real_speed;			//过程速度
	move_reco.location_course_dec = 0;			//过程位置
	move_reco.location_course = real_location;	//过程位置
}

/**
  * 运动重构器速度积分
  * @param  value	加速度
**/
#define Speed_Course_Integral(value)	\
{	\
	move_reco.speed_course_dec += value;												\
	move_reco.speed_course += move_reco.speed_course_dec / CONTROL_FREQ_HZ;		\
	move_reco.speed_course_dec = move_reco.speed_course_dec % CONTROL_FREQ_HZ;	\
}								//(C语言除法运算向0取整，直接取余即可)

/**
  * 运动重构器位置积分
  * @param  value	速度
**/
#define Location_Course_Integral(value)	\
{	\
	move_reco.location_course_dec += value;												\
	move_reco.location_course += move_reco.location_course_dec / CONTROL_FREQ_HZ;		\
	move_reco.location_course_dec = move_reco.location_course_dec % CONTROL_FREQ_HZ;	\
}								//(C语言除法运算向0取整，直接取余即可)
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

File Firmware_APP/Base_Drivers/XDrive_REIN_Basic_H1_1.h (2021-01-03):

/******
	************************************************************************
	******
	** @project : XDrive_Step
	** @brief   : 具有多功能接口和闭环功能的步进电机
	** @author  : unlir (知不知啊)
	** @contacts: QQ.1354077136
	******
	** @address : https://github.com/unlir/XDrive
	******
	** @issuer  : REIN ( 知驭 实验室) (QQ: 857046846)             (discuss)
	** @issuer  : IVES (艾维斯实验室) (QQ: 557214000)             (discuss)
	** @issuer  : X_Drive_Develop     (QQ: Contact Administrator) (develop)
	******
	************************************************************************
	******
	** {Stepper motor with multi-function interface and closed loop function.}
	** Copyright (c) {2020}  {unlir(知不知啊)}
	** 
	** This program is free software: you can redistribute it and/or modify
	** it under the terms of the GNU General Public License as published by
	** the Free Software Foundation, either version 3 of the License, or
	** (at your option) any later version.
	** 
	** This program is distributed in the hope that it will be useful,
	** but WITHOUT ANY WARRANTY; without even the implied warranty of
	** MERCHANTABILITY or FITNESS FOR A PARTICULAR PURPOSE.  See the
	** GNU General Public License for more details.
	** 
	** You should have received a copy of the GNU General Public License
	** along with this program.  If not, see <http://www.gnu.org/licenses/>.
	******
	************************************************************************
******/

/*****
  ** @file     : XDrive_REIN_Basic_H1_0.c/h
  ** @brief    : XDrive_REIN_Basic_H1_0
  ** @versions : newest
  ** @time     : newest
  ** @reviser  : unli (HeFei China)
  ** @explain  : null
*****/

#ifndef XDRIVE_REIN_BASIC_H1_0_H
#define XDRIVE_REIN_BASIC_H1_0_H

#ifdef __cplusplus
extern "C" {
#endif

/********** A **********/
//ADC
#define ADC_POWER_U_GROUP								(0)		//ADC1
#define ADC_POWER_U_CHANNEL							(0)				//第1组
#define ADC_POWER_I_GROUP								(0)		//ADC1
#define ADC_POWER_I_CHANNEL							(1)				//第2组

/********** B **********/
/********** BUTTON **********/
/********** BUTTON **********/
/********** BUTTON **********/
//(GPIO)
#define BUTTON_UP_GPIO_CLK_ENABLE()			__HAL_RCC_GPIOB_CLK_ENABLE();		//PB12
#define BUTTON_UP_GPIO_Port							(GPIOB)
#define BUTTON_UP_Pin 									(GPIO_PIN_12)
#define BUTTON_DOWN_GPIO_CLK_ENABLE()		__HAL_RCC_GPIOB_CLK_ENABLE();		//PB2
#define BUTTON_DOWN_GPIO_Port						(GPIOB)
#define BUTTON_DOWN_Pin 								(GPIO_PIN_2)

/********** C **********/

/********** D **********/

/********** E **********/

/********** F **********/

/********** G **********/

/********** H **********/
/********** HW_ELEC **********/
/********** HW_ELEC **********/
/********** HW_ELEC **********/
//(GPIO)
#define HW_ELEC_AP_GPIO_CLK_ENABLE()		__HAL_RCC_GPIOA_CLK_ENABLE()		//PA5
#define HW_ELEC_AP_GPIO_Port						(GPIOA)
#define HW_ELEC_AP_Pin									(GPIO_PIN_5)
#define HW_ELEC_AM_GPIO_CLK_ENABLE()		__HAL_RCC_GPIOA_CLK_ENABLE()		//PA4
#define HW_ELEC_AM_GPIO_Port						(GPIOA)
#define HW_ELEC_AM_Pin									(GPIO_PIN_4)
#define HW_ELEC_BP_GPIO_CLK_ENABLE()		__HAL_RCC_GPIOA_CLK_ENABLE()		//PA3
#define HW_ELEC_BP_GPIO_Port						(GPIOA)
#define HW_ELEC_BP_Pin									(GPIO_PIN_3)
#define HW_ELEC_BM_GPIO_CLK_ENABLE()		__HAL_RCC_GPIOA_CLK_ENABLE()		//PA2
#define HW_ELEC_BM_GPIO_Port						(GPIOA)
#define HW_ELEC_BM_Pin									(GPIO_PIN_2)
//(AFIO & TIM)
#define HW_ELEC_APWM_GPIO_CLK_ENABLE()	__HAL_RCC_GPIOB_CLK_ENABLE()		//PB11
#define HW_ELEC_APWM_GPIO_Port					(GPIOB)
#define HW_ELEC_APWM_Pin								(GPIO_PIN_11)
#define HW_ELEC_APWM_CHANNEL						(TIM_CHANNEL_4)
#define HW_ELEC_BPWM_GPIO_CLK_ENABLE()	__HAL_RCC_GPIOB_CLK_ENABLE()		//PB10
#define HW_ELEC_BPWM_GPIO_Port					(GPIOB)
#define HW_ELEC_BPWM_Pin								(GPIO_PIN_10)
#define HW_ELEC_BPWM_CHANNEL						(TIM_CHANNEL_3)
#define HW_ELEC_PWM_TIM_CLK_ENABLE()		__HAL_RCC_TIM2_CLK_ENABLE()			//TIM2
#define	HW_ELEC_PWM_Get_TIM							(TIM2)
#define	HW_ELEC_PWM_Get_HTIM						(htim2)
#define	HwElec_TIM_AFIO_REMAP						__HAL_AFIO_REMAP_TIM2_PARTIAL_2();	//TIM_AFIO端口重新映射

/********** I **********/

/********** J **********/

/********** K **********/

/********** L **********/

/********** M **********/
/********** MT6816 **********/
/********** MT6816 **********/
/********** MT6816 **********/
//MT6816_SPI采集(GPIO)
#define MT6816_SPI_CS_GPIO_CLK_ENABLE()		__HAL_RCC_GPIOA_CLK_ENABLE()	//PA15
#define MT6816_SPI_CS_GPIO_Port						(GPIOA)
#define MT6816_SPI_CS_Pin 								(GPIO_PIN_15)
//MT6816_SPI采集(AFIO & SPI)
#define MT6816_SPI_CLK_GPIO_CLK_ENABLE()	__HAL_RCC_GPIOB_CLK_ENABLE()	//PB3
#define MT6816_SPI_CLK_GPIO_Port					(GPIOB)
#define MT6816_SPI_CLK_Pin 								(GPIO_PIN_3)
#define MT6816_SPI_MISO_GPIO_CLK_ENABLE()	__HAL_RCC_GPIOB_CLK_ENABLE()	//PB4
#define MT6816_SPI_MISO_GPIO_Port					(GPIOB)
#define MT6816_SPI_MISO_Pin 							(GPIO_PIN_4)
#define MT6816_SPI_MOSI_GPIO_CLK_ENABLE()	__HAL_RCC_GPIOB_CLK_ENABLE()	//PB5
#define MT6816_SPI_MOSI_GPIO_Port					(GPIOB)
#define MT6816_SPI_MOSI_Pin 							(GPIO_PIN_5)
#define MT6816_SPI_SPI_CLK_ENABLE()				__HAL_RCC_SPI1_CLK_ENABLE();	//SPI1
#define MT6816_SPI_Get_SPI								(SPI1)
#define MT6816_SPI_Get_HSPI								(hspi1)
#define	MT6816_SPI_AFIO_REMAP							__HAL_AFIO_REMAP_SPI1_ENABLE();	//SPI1_AFIO端口重新映射
#define	MT6816_SPI_Prescaler							(SPI_BAUDRATEPRESCALER_8)				//SPI1_8分频_9M
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

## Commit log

2020-09-23 开发测试 F1.1.4.1 2020/9/24 4:34
2020-11-08 UI界面更新
2020-11-17 (XDrive H1.1) / (XDriveBL F1.1) / (XDriveAPP H1.1.5)
    [XDrive_bom.xlsx]
2020-11-18 (XDrive H1.1) / (XDriveBL F1.1) / (XDriveAPP F1.1.5) 第1次修订
    [XDrive_bom.xlsx]
2020-11-18 (XDrive H1.1) / (XDriveBL F1.1) / (XDriveAPP F1.1.5) 第2次修订
2020-11-30 (XDrive H1.1b) / (XDriveBL F1.1) / (XDriveAPP F1.1.5) 第3次修订，对PCB3项细节进行了调整，增加了原理图文件，增加了外壳机械图纸
    [XDrive_bom.xlsx, 底座-20201125.STL, 底座.SLDPRT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]
2021-01-06 修改了README.md并更新了几张XDrive的照片
2021-01-18 修正了一个手册中（XDrive explore.pdf）的版本号错误
2021-02-07 增加启动校准时进入校准界面
2021-04-14 添加XDrive_H1.1b PCB工程
    [Drive.SchDoc, MCU.SchDoc, Port.SchDoc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]
2022-12-30 增加3群
